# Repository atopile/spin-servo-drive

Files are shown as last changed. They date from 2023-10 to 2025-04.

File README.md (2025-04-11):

# Servos are dope.

Compared to the steppers we stick on our 3D printers, CNC machines and paintball turrets:
 - They're way faster 🏃
 - Far more powerful (higher torque for longer) 💪
 - More accurate (higher resolution) 🎯
 - And they're closed loop (they know where they are) 🤖

The only downside is that they're expensive, like hundreds of dollars.

Introducing spin ✨ - the $30 servo for the masses (designed with atopile)

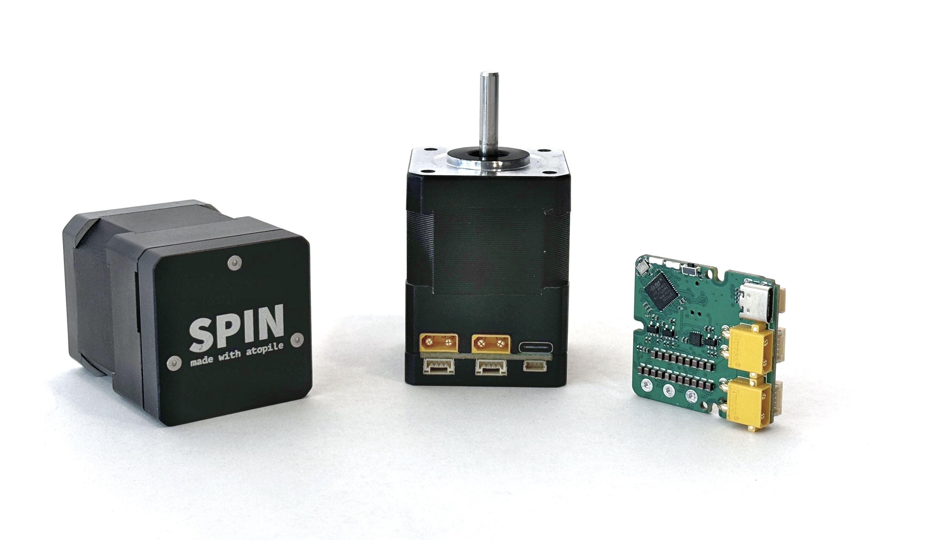
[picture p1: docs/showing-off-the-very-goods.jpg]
spin


## Wiggle wiggle wiggle

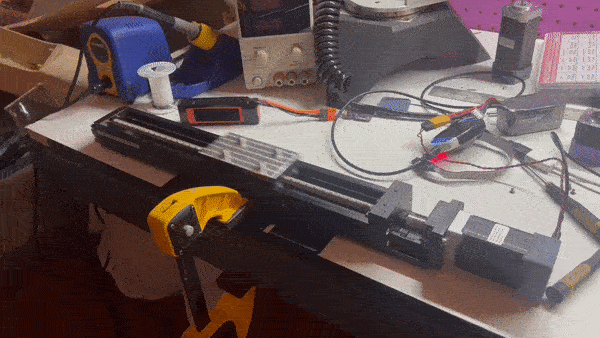
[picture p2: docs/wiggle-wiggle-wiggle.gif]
wiggle-wiggle-wiggle


## Build your own Spin Servo Motor Drive

This project is fully open source and designed with [atopile](https://github.com/atopile/atopile), a new language and compiler to design electronics with code.

## Goals + (default) Specs

- Obviously better option than stepper motors for 3D printers, CNC machines and robotics
- Open-source design that is easy to:
  - contribute to
  - fork maintainable derivatives of
  - robust

- 2x CAN comms with JST-GH connectors
- XT30 power connector
- 0.25Nm continuous rated torque (0.75Nm peak)
- <0.1° resolution
- 12V-24V input voltage

## Getting started

This project was written in `ato`, a new electronics description language we are developing to help create and share electronic designs. Get started here: https://atopile.io/

### Electronics

**Write me please!**

### Firmware

Install [PlatformIO](https://platformio.org/) into VSCode. It has the utilities to build, upload and debug the firmware.

You may also need to install `libusb` (eg. `brew install libusb` on OSx) to run the build!

There are a few build configurations:
- `debug` is intended as a JTAG configuration and includes symbols to run the debugger.
- `dfu-manual` uses the GNU command-line dfu-utility to trigger the upload via USB (**Recommended USB workflow**)
- `dfu` uses the built-in PlatformIO dfu utility to program via USB (which **I struggled with on OSx**)

To run a build either use the sidebar (easiest IMO) or PlatformIO CLI (`pio run --help`).

#### Side-bar

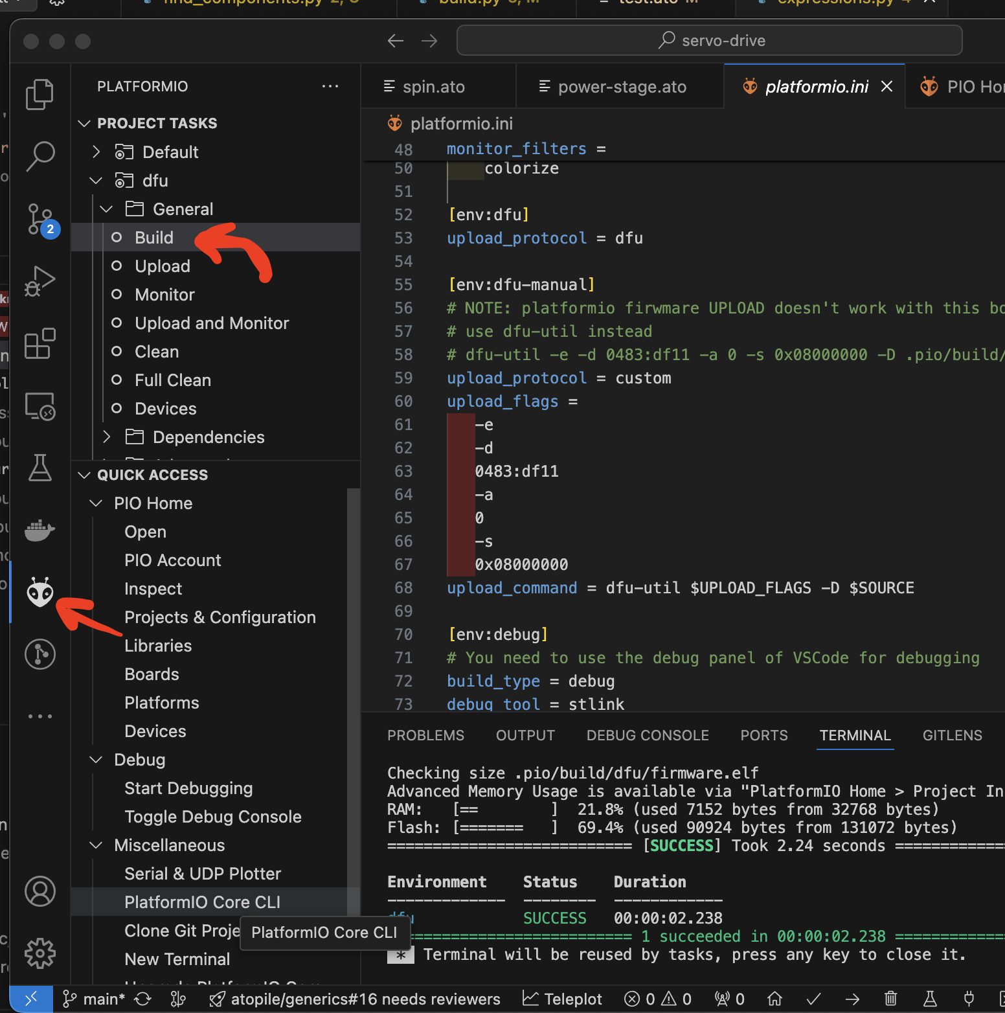
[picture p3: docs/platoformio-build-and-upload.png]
platformio


#### CLI

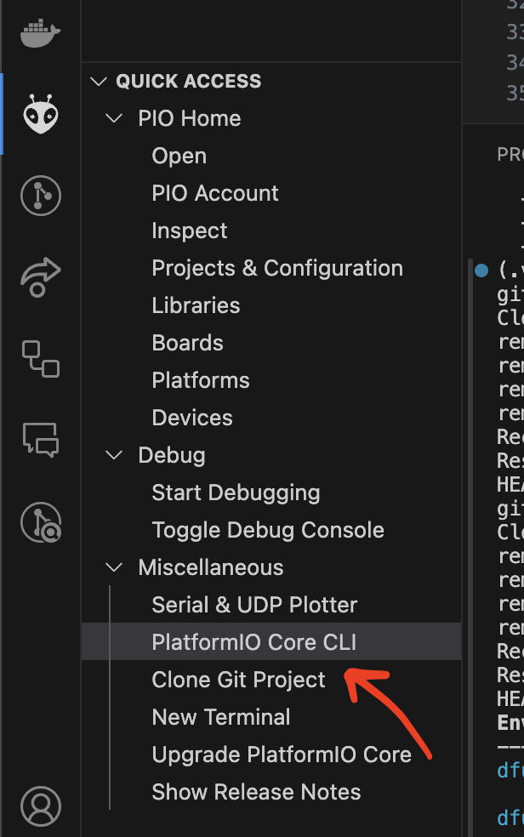
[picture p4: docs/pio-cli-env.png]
platformio-cli


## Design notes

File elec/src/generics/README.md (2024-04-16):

# Generics

## Overview

Standard libaries for use in your projects. These include:

- **Resistors**
- **Capacitors**
- **Inductors**
- **Diodes**
- **Transistors**
- **Interfaces**

## Installation
Run in the terminal:

```ato install generics``

Add to your ato project:

- Resistors   ```import Resistor from "generics/resistor.ato```
- Capacitors  ```import Capacitor from "generics/capacitor.ato```
- Inductors   ```import Inductor from "generics/inductor.ato```
- Interfaces  ```import Interface from "generics/interface.ato```
- etc...

## Features
### Resistors
The standard libary includes several thousand resistor options. In your ato project, simply specify any requirements and the best resistor will be automatically selected.
Example:

```import Resistor from "generics/resistor.ato"```
```myResistor = new Resistor```
```myResistor.value = 1000```
```myResistor.footprint = "R0402"```
```myResistor.tolerance = 10```

The solver will find a resistor that has a resistance between 900 and 1100 ohms accounting for tolerance, and a footprint of R0402.

### Capacitors
Similar to resistors, just specify the value and footprint and the solver will find the best capacitor for your application.

### Inductors
Currently not supported for automatic selection, but you can install any inductor you like using '''ato install''' and then use it in your project.

We strongly reccomend using subclassing for new components, something like this:

```import Inductor from "generics/inductor.ato"```
```component MyInductor from Inductor:```
```    value = 1000```
```    footprint = "L0402" ```

Then you can use it in your project like this:

```import MyInductor from "myInductor.ato"```
```myInductor = new MyInductor```
```myInductor.value = 1000```
```myInductor.footprint = "L0402"```

### Interfaces
Interfaces standardize the way you connect to modules. By implementing an interface from the standard libary, you can be sure that your module will be compatible with any other module that implements the same interface. This makes it easy to share modules between projects and be sure that they will work together.

## Contributing

We welcome contributions and suggestions to improve this module. Please submit your contributions as pull requests on our GitHub repository.

## License

This package documentation is provided under the [MIT License](#).

## Contact

For further inquiries or support, please contact us at [email@example.com](mailto:email@example.com).

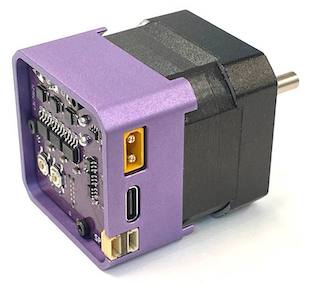
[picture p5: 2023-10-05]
docs/showing-off-the-goods.jpg

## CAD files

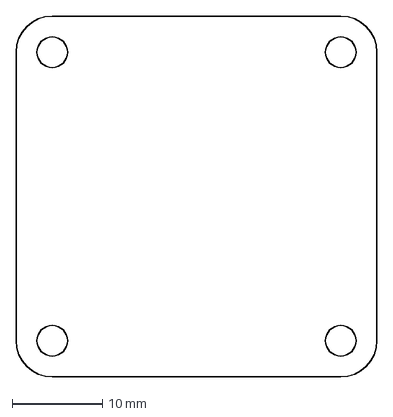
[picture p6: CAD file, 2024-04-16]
elec/src/programming-headers/mech/template_40x40 2.dxf
40.0 x 40.0 mm

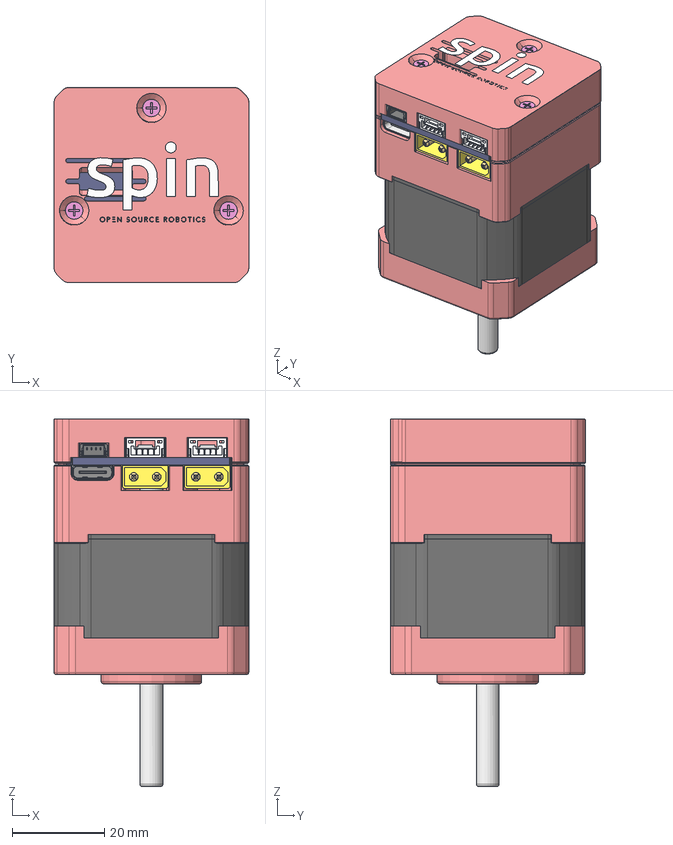
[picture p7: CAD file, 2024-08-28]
mech/SPIN.step
42.3 x 42.4 x 82.6 mm
shaft
motor_housing
lid x 2
JST SH, 4 Pin v2
Amass_XT30PW-M_pcb solder x 2
ConPins
PcbPins
Mold
Frame
SM04B-GHS-TB x 2
magnet
M2x14 x 3
hex_socket_button_head_M3x40 x 4

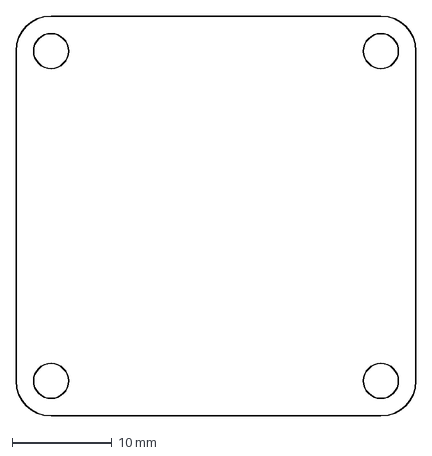
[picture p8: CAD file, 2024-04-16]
elec/src/saleae-header/mech/template_outline.dxf
40.0 x 40.0 mm

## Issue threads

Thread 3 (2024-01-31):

Buck gets hot + should be replaced with the one from the regulators lib

mawildoer, 2024-01-31:
It's commented out as of now, but needs to be reinstated https://github.com/atopile/spin-servo-drive/pull/2/files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

mawildoer, 2024-03-07:
Requires validation; have debug build of that

napowderly, 2024-05-02:
Inductor sized incorrectly on first build, updated in next rev.

Closed 2024-05-02.

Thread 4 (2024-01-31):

Boot button should enable DFU

napowderly, 2024-01-31:
Currently the boot selection pin is used for I2C, need to find a better pinout

napowderly, 2024-05-02:
Fixed, holding button on boot will enter DFU

Closed 2024-05-02.

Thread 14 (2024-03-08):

CAN on wrong micro pins

mawildoer, 2024-03-08:
CAN can't work on these pins and they don't match where we previously had it

https://www.st.com/resource/en/datasheet/stm32g431c6.pdf#page=56

```
    # CANBUS Comms
    can_ttl.rx ~ ic.PB5
    can_ttl.tx ~ ic.PB6
```

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

napowderly, 2024-05-02:
Updated in beta build

Closed 2024-05-02.

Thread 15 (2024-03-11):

Current sense not working

napowderly, 2024-03-11:
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

Moved phase C to PA3 and seems to be working well

napowderly, 2024-05-02:
Pinout updated

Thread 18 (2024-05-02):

CAN bus control - Position, Velocity, Torque

napowderly, 2024-05-02:
Objective: Build a simple interface to send commands + receive status messages from motors.

SimpleFOC has a commander interface that will currently take serial commands
https://docs.simplefoc.com/commander_interface

Want to be as standard as possible, a few possible standards to follow/integrate with:
https://opencyphal.org/
https://legacy.uavcan.org/Specification/7._List_of_standard_data_types/
https://docs.odriverobotics.com/v/0.5.4/commands.html
https://github.com/mjbots/moteus/blob/main/docs/reference.md

mawildoer, 2024-07-18:
Selected CANSimple. Implementing w/ #37

Closed 2024-07-18.

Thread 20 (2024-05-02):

Change position sensor to something more available

napowderly, 2024-05-02:
MA732 has been a little hard to source

current sensor:
14-bit, 60krpm, $2~$5 (unstable) 0 stock
https://jlcpcb.com/partdetail/Monolithic_PowerSystems-MA732GQZ/C3824836

a few alternatives:

21-Bit, 120krpm, $3.89, 1k+ stock
https://jlcpcb.com/partdetail/MagnTek-MT6835GTSTD/C2932578

14-bit, 25krpm, $2.04, 1k+ stock
https://jlcpcb.com/partdetail/MagnTek-MT6816CTSTD/C2925077

14-bit, 28krpm, $3.08, 800 stock
https://jlcpcb.com/partdetail/Ams-AS5047PATSM/C962063

Closed 2024-07-18.

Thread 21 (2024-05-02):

CAN address enumeration

napowderly, 2024-05-02:
Goal: super quickly enumerate devices, ideally without flashing new FW or requiring PC connection.

Imagining with button + LEDs, the user could toggle between colors representing different addresses. The state should be saved in non-volatile memory, so the address is preserved after power cycling.

This would be useful for applications where the user writes controller code on an RPI or Arduino and wants an easy way to reference the motors.

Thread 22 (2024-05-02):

Motion profiles

napowderly, 2024-05-02:
For applications like 3D printers and CNC machines, having a lookahead feature on the controller that can then send the next series of points to the servo could be neat.

Copper280Z has been playing around with a Klipper integration for SimpleFOC, could be a good starting place.

mawildoer, 2024-07-18:
Depends on #37

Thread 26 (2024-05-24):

Manually test current sense

napowderly, 2024-05-24:
Manual validation of current sensor.

Procedure:
1. Directly attach wires across shunt
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

2. Source current with PSU

4. Measure output of opamp circuit with Saleae

5. Read ADC value from micro

Phase A:
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

Phase B:

Phase C:

Closed 2024-07-18.

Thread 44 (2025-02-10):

Am I missing something!

kzali, 2025-02-10:
Is the motor a modified Nema 17 motor or a an actual BLDC motor? And how are the 3 phases wired?

mawildoer, 2025-02-11:
It's an actual BLDC motor in a NEMA 17 frame, which is frequently also used for stepper motors

@napowderly may know how the 3 phases are wired

kzali, 2025-02-11:
thanks that makes sense.  Great work

Closed 2025-02-11.

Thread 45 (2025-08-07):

It is posible to used pmsm motor 220v??

artayasa, 2025-08-07:
Hi mate interestjng with your project, its posible to used for ac servo pmsm 220v with coustem hardware??

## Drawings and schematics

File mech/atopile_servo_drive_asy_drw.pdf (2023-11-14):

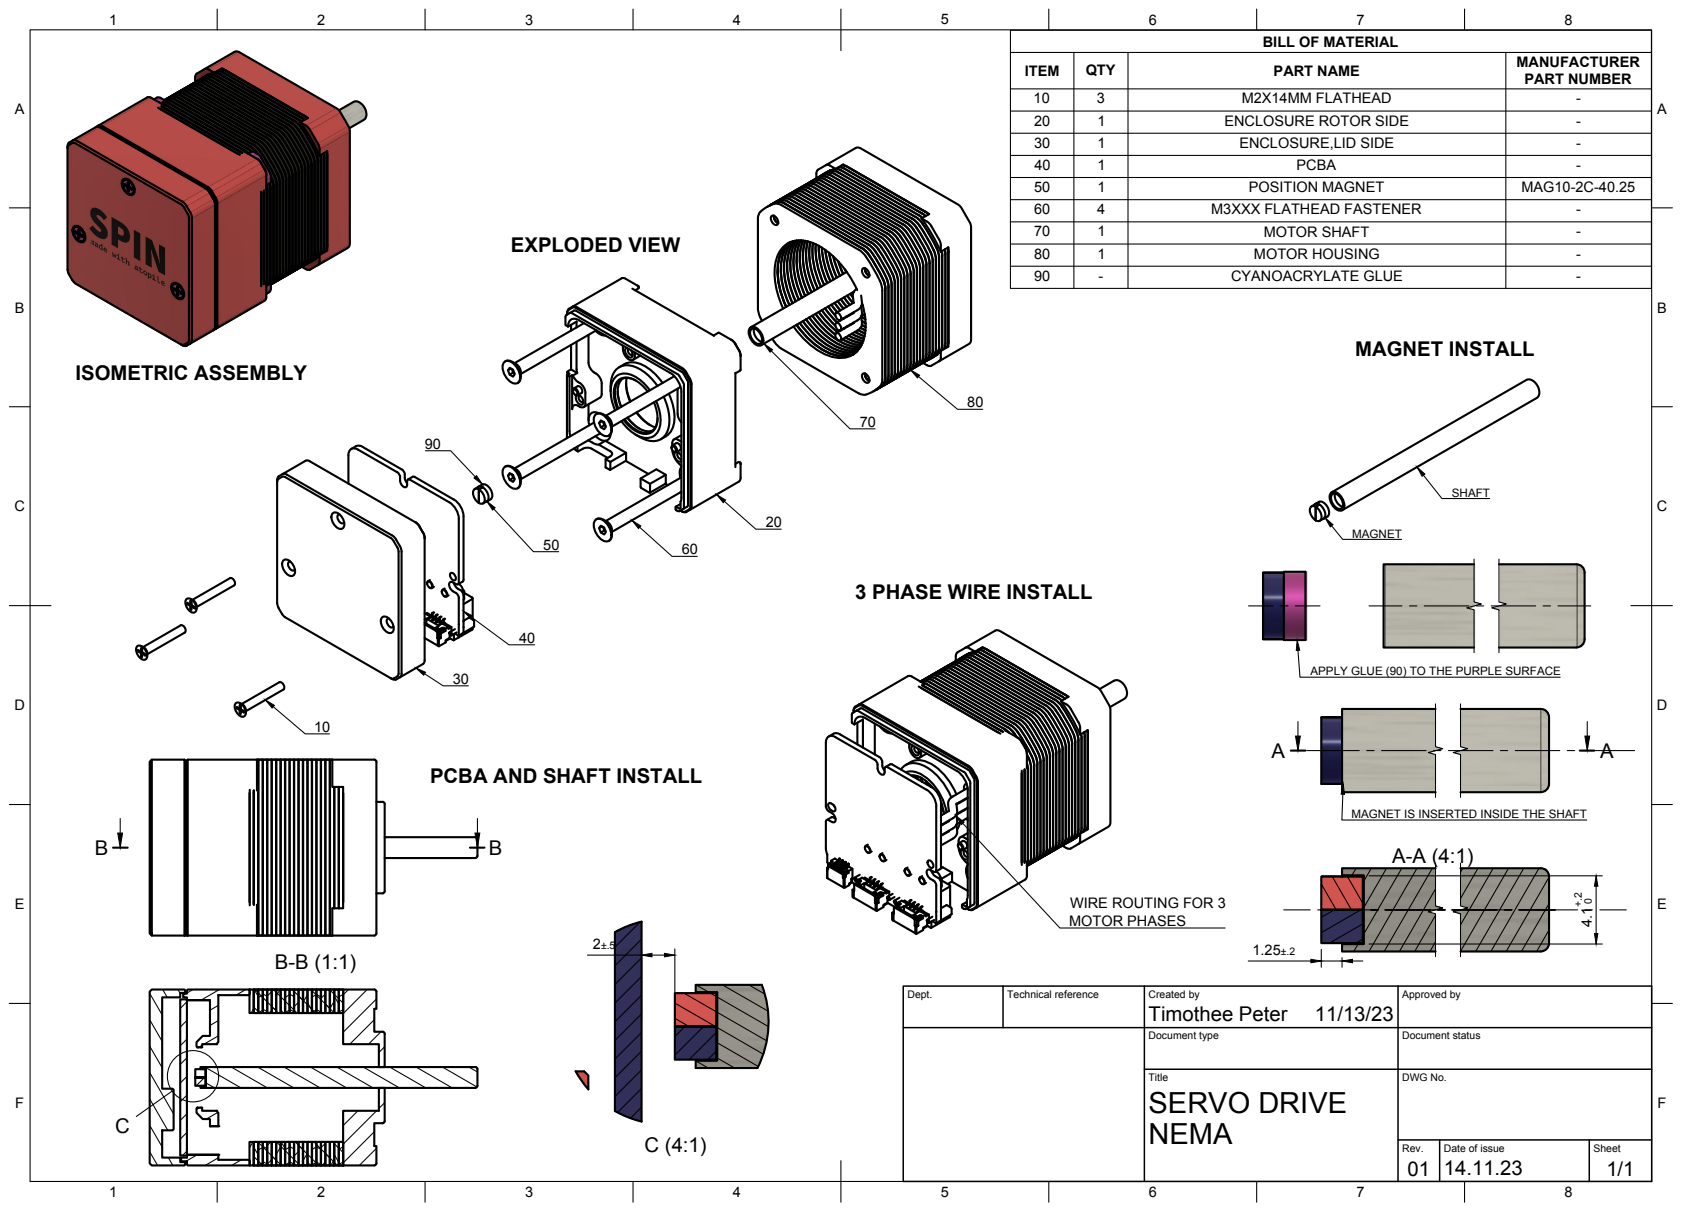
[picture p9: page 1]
Title; DWG No.; Rev.; Date of issue; Sheet; SERVO DRIVE; ITEM; QTY; PART NAME; MANUFACTURER; PART NUMBER; M2X14MM FLATHEAD; ENCLOSURE ROTOR SIDE; ENCLOSURE,LID SIDE; PCBA; POSITION MAGNET; MAG10-2C-40.25; M3XXX FLATHEAD FASTENER; MOTOR SHAFT; MOTOR HOUSING; CYANOACRYLATE GLUE; WIRE ROUTING FOR 3; MOTOR PHASES; MAGNET INSTALL; EXPLODED VIEW; ISOMETRIC ASSEMBLY

BILL OF MATERIAL

3 PHASE WIRE INSTALL

APPLY GLUE (90) TO THE PURPLE SURFACE

PCBA AND SHAFT INSTALL

MAGNET IS INSERTED INSIDE THE SHAFT

Dept. | Technical reference | Created by Timothee Peter 11/13/23 | Approved by

Document type | Document status

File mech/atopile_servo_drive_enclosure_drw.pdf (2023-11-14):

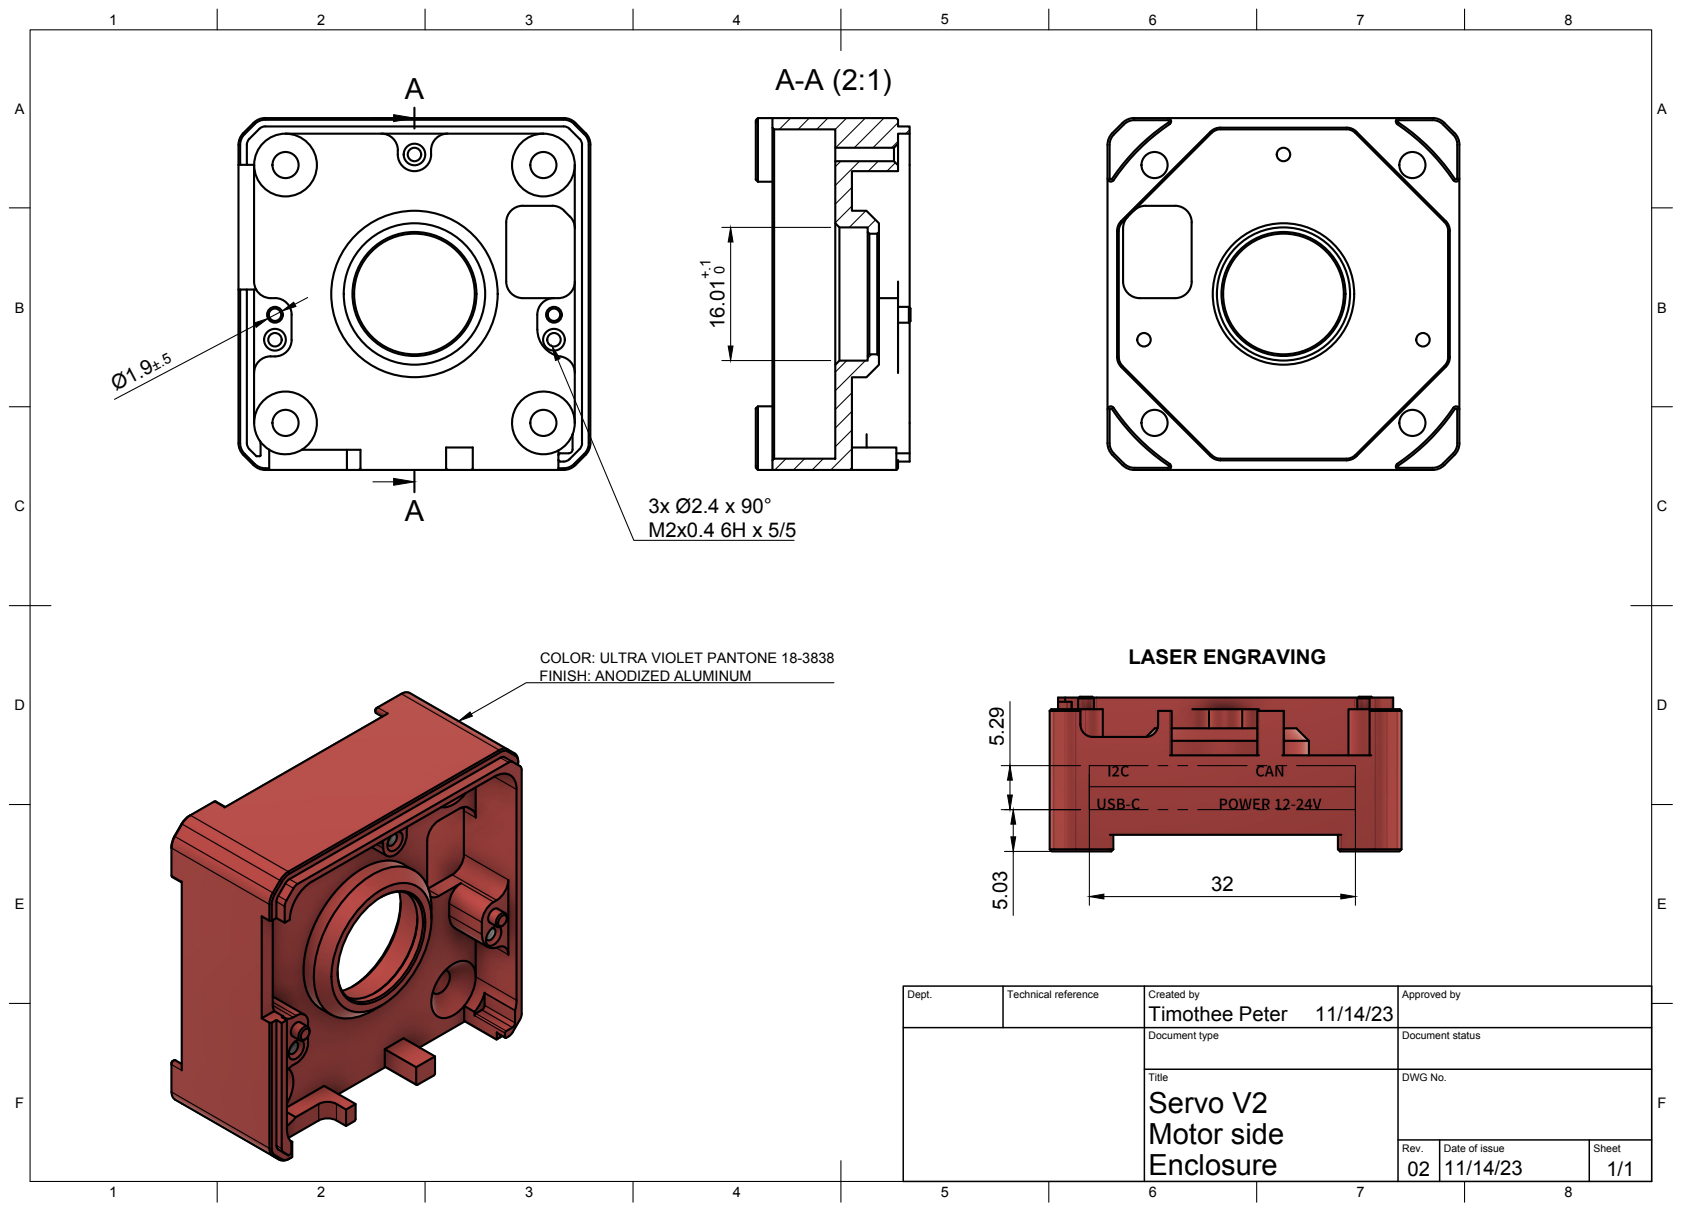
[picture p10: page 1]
Title; DWG No.; Rev.; Date of issue; Sheet; Motor side; Servo V2; LASER ENGRAVING

COLOR: ULTRA VIOLET PANTONE 18-3838
FINISH: ANODIZED ALUMINUM

Dept. | Technical reference | Created by Timothee Peter 11/14/23 | Approved by

Document type | Document status

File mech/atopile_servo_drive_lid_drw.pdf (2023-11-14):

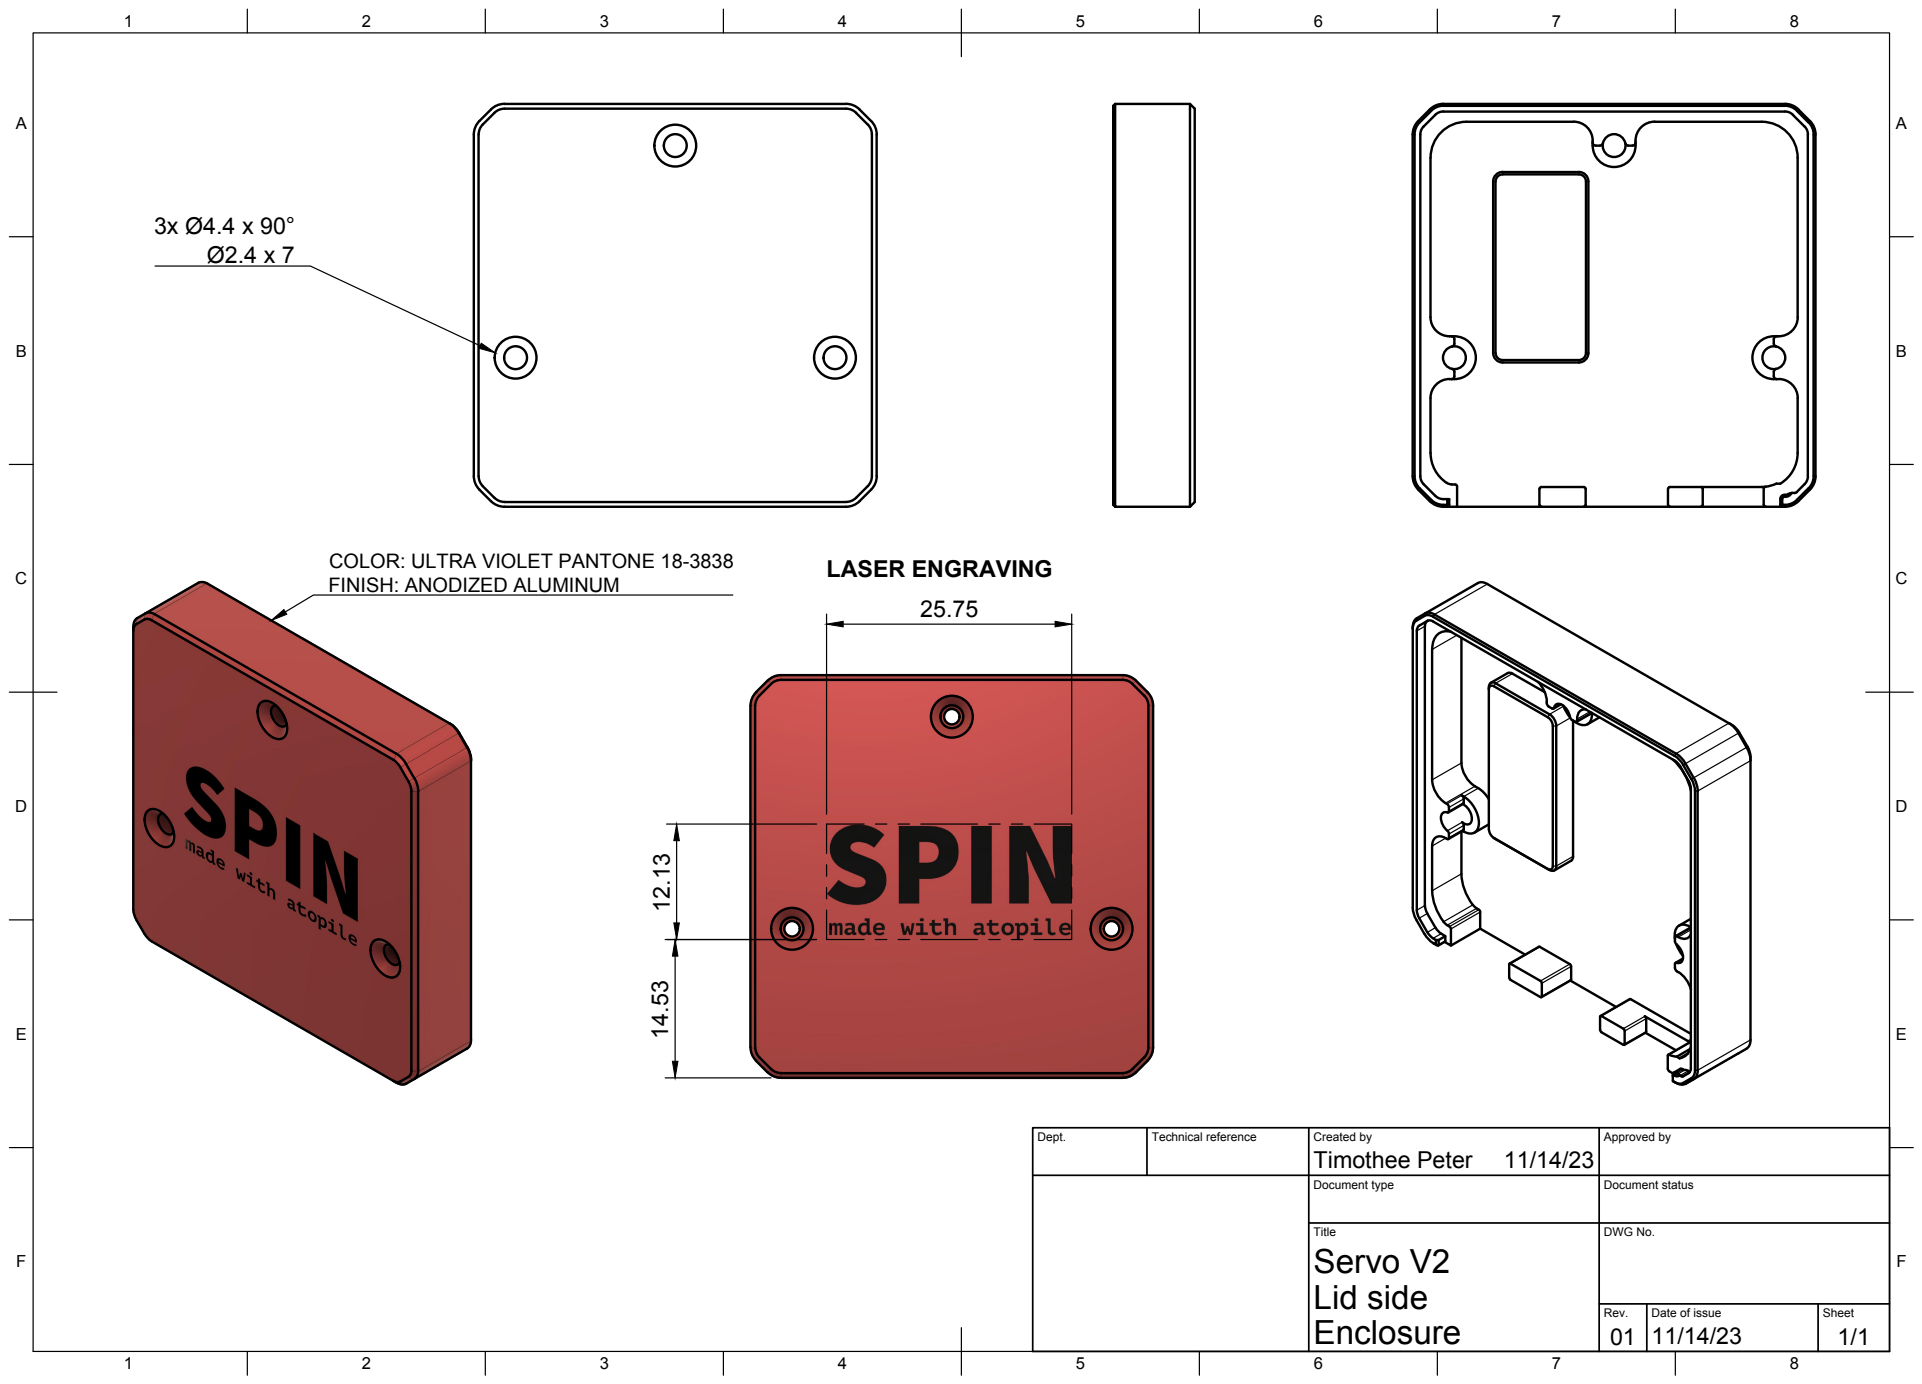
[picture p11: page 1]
Title; DWG No.; Rev.; Date of issue; Sheet; Lid side; Servo V2; COLOR: ULTRA VIOLET PANTONE 18-3838; LASER ENGRAVING

FINISH: ANODIZED ALUMINUM

Dept. | Technical reference | Created by Timothee Peter 11/14/23 | Approved by

Document type | Document status

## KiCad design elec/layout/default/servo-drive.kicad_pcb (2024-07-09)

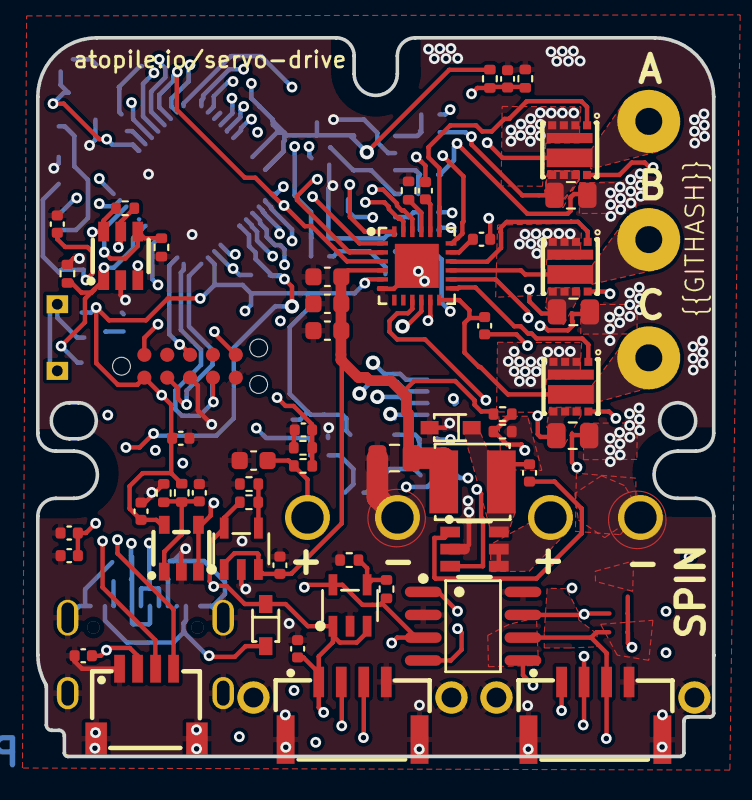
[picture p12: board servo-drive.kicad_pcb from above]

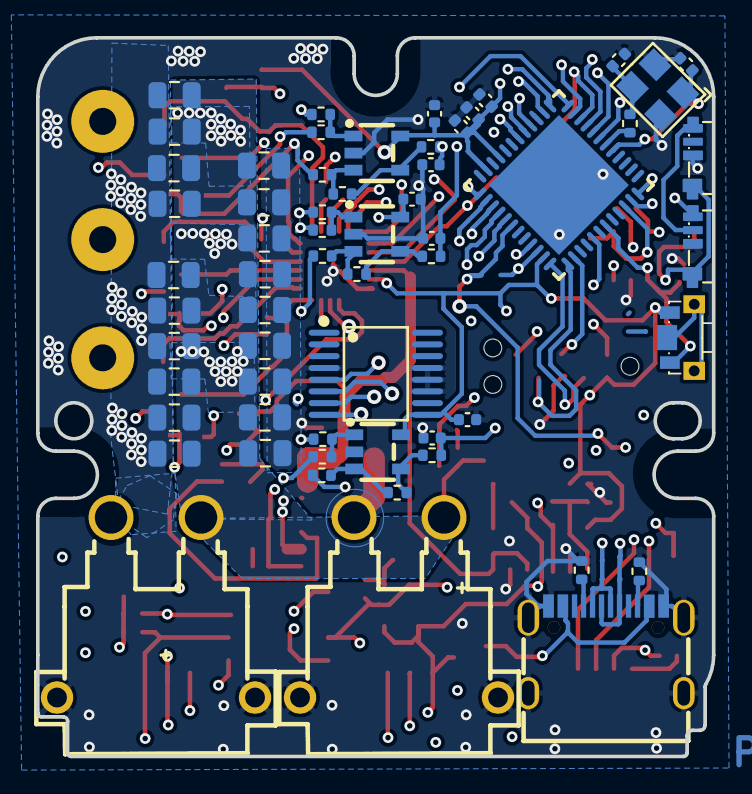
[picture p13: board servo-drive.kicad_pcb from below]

Board: 4 copper layers, 37.6 x 39.9 mm, 125 parts (60 on the bottom side), 80 nets.

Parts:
C1: 10V 10uF X5R ±10% 0603 Multilayer Ceramic Capacit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; C0603
C2, C13, C16, C17, C18, C19, C24, C28, C40, C51: 16V 100nF X7R ±10% 0402 Multilayer Ceramic Capaci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; C0402
C3, C4, C6, C20, C21, C22, C25, C26, C27, C29, C30, C35, C36, C37, C38, C39, C47, C48, C49: C0805
C5, C7, C9, C14, C15, C33, C34, C41, C43, C45, C50: 25V 1uF X5R ±10% 0402 Multilayer Ceramic Capacito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; C0402
C8: 25V 10uF X5R ±10% 0805 Multilayer Ceramic Capacit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; C0805
C10, C11, C12: 50V 2.2nF X7R ±10% 0402 Multilayer Ceramic Capaci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; C0402
C23, C31, C32: 16V 4.7uF X5R ±10% 0603 Multilayer Ceramic Capaci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; C0603
C42, C44: 50V 22pF C0G ±5% 0402 Multilayer Ceramic Capacito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; C0402
J1: USB-C-SMD_KH-TYPE-C-16P
R1, R15, R20, R38: 62.5mW Thick Film Resistors 50V ±100ppm/℃ ±1% 10k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; R0402
R2, R6, R13, R25, R44, R48, R50: 62.5mW Thick Film Resistors 50V ±100ppm/℃ ±1% 1kΩ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; R0402
R3: 62.5mW Thick Film Resistors 50V ±100ppm/℃ ±1% 100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; R0402
R4, R8, R47: 3mΩ +/- 1%; R0805
R5, R9: 62.5mW Thick Film Resistors 50V ±100ppm/℃ ±1% 5.1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; R0402
R7: 62.5mW Thick Film Resistors 50V ±100ppm/℃ ±1% 200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; R0402
R10: 62.5mW Thick Film Resistors 50V ±100ppm/℃ ±1% 27.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; R0402
R11: 62.5mW Thick Film Resistors 50V ±100ppm/℃ ±1% 3kΩ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; R0402
R12, R14, R26, R45, R49, R51: 62.5mW Thick Film Resistors 50V ±100ppm/℃ ±1% 47k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; R0402
R16, R46, R52: 62.5mW Thick Film Resistors 50V -200ppm/℃~+500ppm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; R0402
R17: 62.5mW Thick Film Resistors 50V ±100ppm/℃ ±1% 20.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; R0402
R18: 62.5mW Thick Film Resistors 50V ±1% ±200ppm/℃ 6.3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; R0402
R19: 10kohm +/- 1%; R0402
R21: 62.5mW Thick Film Resistors 50V ±100ppm/℃ ±1% 11.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; R0402
R22: 62.5mW Thick Film Resistors 50V ±100ppm/℃ ±1% 6.2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; R0402
R29: 62.5mW Thick Film Resistors 50V ±100ppm/℃ ±1% 41.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; R0402
R30: 62.5mW Thick Film Resistors 50V ±100ppm/℃ ±1% 4.3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; R0402
R31: 62.5mW Thick Film Resistors 50V ±100ppm/℃ ±1% 43k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; R0402
U1, U3, U28: V-DFN3030-8K_L3.0-W3.0-P0.65-BL
U2, U14: CONN-TH_XT30PW-M
U4, U20, U21, U24: SOT-23-5_L3.0-W1.7-P0.95-LS2.8-BR
U5, U32: LED-SMD_4P-L4.0-W1.4_SK6805SIDE-S
U6, U18: SOT-23-6_L2.9-W1.6-P0.95-LS2.8-BR
U7, U8, U9: OutputPad
U10: IND-SMD_L4.0-W4.0
U11: KEY-SMD_SKTDLDE010
U12: VQFN-24_L4.0-W4.0-P0.50-TL-EP2.5
U13: UFQFPN-48_L7.0-W7.0-P0.50-BL-EP
U15: CONN-SMD_4P-P1.00_SM04B-SRSS-TB-LF-SN
U16: TAG-CONNECT_TC2050-IDC
U17, U19, U31, U33, U34, U35: NetTie-2_SMD_Pad0.25mm
U22, U23: SOT-23-5_L3.0-W1.7-P0.95-LS2.8-BL
U25: SOIC-8_L4.9-W3.9-P1.27-LS6.0-BL
U26, U27: CONN-SMD_4P-P1.25_SM04B-GHS-TB-LF-SN
U29: TSSOP-16_L5.0-W4.4-P0.65-LS6.4-BL
U30, U36: SOD-323_L1.8-W1.3-LS2.5-RD
U37: OSC-SMD_4P-L3.2-W2.5-BL

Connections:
anchor: U11.3, U11.4
canh: U25.7, U26.2, U27.2
canl: U25.6, U26.3, U27.3
cb: C24.1, U6.1
cc1: J1.A5, R5.1
cc2: J1.B5, R9.1
cs: U13.25, U29.8
dm: J1.A7, J1.B7, U13.33
dp: J1.A6, J1.B6, U13.34
ios.led1-vcc: U5.3, U32.4
micro-miso: U13.27, U29.5
micro-mosi: U13.28, U29.6
micro-sda: U13.30, U15.3
micro-vcc: U5.4, U13.29
micro-vcc-1: R20.2, U11.1, U13.43, U18.1
micro-vcc-2: C28.1, R15.2, R19.1, U13.12
micro-vcc-3: C19.1, R10.2, R11.1, U13.13
micro.micro-io: R2.1, U13.46, U18.4
micro.micro-io-1: R3.1, U13.14, U18.6
micro.micro.ic-vcc-1: C42.1, U13.5, U37.1
pf1_osc_out: R7.1, U13.6
power_stage-gnd: C1.2, C2.2, C3.2, C4.2, C5.2, C6.2, C7.2, C8.2, C9.2, C10.2, C11.2, C12.2, C13.2, C14.2, C15.2, C16.2, C17.2, C18.2, C19.2, C20.2, C21.2, C22.2, C23.2, C25.2, C26.2, C27.2, C28.2, C29.2, C30.2, C31.2, C32.2, C33.2, C34.2, C35.2, C36.2, C37.2, C38.2, C39.2, C40.2, C42.2, C44.2, C47.2, C48.2, C49.2, C50.2, C51.2, J1.1, J1.2, J1.3, J1.4, J1.A1, J1.A12, J1.B1, J1.B12, R2.2, R4.2, R5.2, R8.2, R9.2, R11.2, R18.2, R19.2, R20.1, R22.2, R30.2, R31.2, R38.2, R47.2, U2.1, U2.3, U2.4, U4.2, U5.2, U6.2, U12.6, U12.25, U13.49, U14.1, U14.3, U14.4, U15.1, U15.5, U15.6, U16.3, U16.5, U18.2, U19.2, U20.2, U21.2, U22.2, U23.2, U24.2, U25.2, U25.8, U26.4, U26.5, U26.6, U27.4, U27.5, U27.6, U29.4, U29.11, U29.12, U29.13, U32.2, U33.2, U35.2, U36.2, U37.2, U37.4
power_stage-vcc: C1.1, C3.1, C4.1, C6.1, C20.1, C21.1, C22.1, C25.1, C26.1, C27.1, C29.1, C30.1, C35.1, C36.1, C37.1, C38.1, C39.1, C47.1, C48.1, C49.1, R10.1, U1.2, U1.3, U1.4, U1.10, U2.2, U3.2, U3.3, U3.4, U3.10, U6.4, U6.5, U14.2, U28.2, U28.3, U28.4, U28.10
power_stage-vcc-1: C5.1, C8.1, C23.1, C31.1, C32.1, R29.1, U10.2, U12.4, U22.1, U22.3
power_stage-vcc-2: C7.1, C13.1, C15.1, C16.1, C17.1, C18.1, C40.1, C50.1, C51.1, R1.1, R3.2, R15.1, R21.1, U4.5, U11.2, U12.5, U13.20, U13.21, U13.23, U13.35, U13.48, U15.2, U16.1, U18.5, U20.5, U21.5, U23.5, U24.5, U25.3, U29.9
power_stage.gate_driver.ic-vcc: C41.1, U12.20
power_stage.gate_driver.ic-vcc-1: C43.1, U12.17
power_stage.gate_driver.ic-vcc-2: C45.1, U12.14
power_stage.gate_driver.ic-vcc-3: R31.1, U12.21
power_stage.phase_a-vcc: U12.1, U12.22, U13.8
power_stage.phase_a.current_sensor-vcc: R14.2, R45.2, R51.2, U4.3, U4.4
power_stage.phase_a.current_sensor-vcc-1: C10.1, R16.2, U13.17
power_stage.phase_a.current_sensor.net_tie_n-_shunt_n: R6.1, U19.1
power_stage.phase_a.current_sensor.net_tie_p-_shunt_p: R13.1, U17.1
power_stage.phase_a.current_sensor.opamp-gnd: R12.2, R16.1, U20.4
power_stage.phase_a.current_sensor.opamp-inverting: R6.2, R12.1, U20.3
power_stage.phase_a.current_sensor.opamp-non_inverting: R13.2, R14.1, U20.1
power_stage.phase_a.half_bridge-gnd: R4.1, U17.2, U28.5, U28.6, U28.7
power_stage.phase_a.half_bridge-io: C41.2, U7.1, U12.18, U28.9
power_stage.phase_a.half_bridge-vcc: U12.19, U28.1
power_stage.phase_a.half_bridge-vcc-1: U12.11, U28.8
power_stage.phase_b-vcc: U12.2, U12.23, U13.9
power_stage.phase_b.current_sensor-vcc: C11.1, R46.2, U13.18
power_stage.phase_b.current_sensor.net_tie_n-_shunt_n: R25.1, U33.1
power_stage.phase_b.current_sensor.net_tie_p-_shunt_p: R44.1, U31.1
power_stage.phase_b.current_sensor.opamp-gnd: R26.2, R46.1, U21.4
power_stage.phase_b.current_sensor.opamp-inverting: R25.2, R26.1, U21.3
power_stage.phase_b.current_sensor.opamp-non_inverting: R44.2, R45.1, U21.1
power_stage.phase_b.half_bridge-gnd: R8.1, U1.5, U1.6, U1.7, U31.2
power_stage.phase_b.half_bridge-io: C43.2, U1.9, U8.1, U12.15
power_stage.phase_b.half_bridge-vcc: U1.1, U12.16
power_stage.phase_b.half_bridge-vcc-1: U1.8, U12.10
power_stage.phase_c-vcc: U12.3, U12.24, U13.10
power_stage.phase_c.current_sensor-vcc: C12.1, R52.2, U13.11
power_stage.phase_c.current_sensor.net_tie_n-_shunt_n: R48.1, U35.1
power_stage.phase_c.current_sensor.net_tie_p-_shunt_p: R50.1, U34.1
power_stage.phase_c.current_sensor.opamp-gnd: R49.2, R52.1, U24.4
power_stage.phase_c.current_sensor.opamp-inverting: R48.2, R49.1, U24.3
power_stage.phase_c.current_sensor.opamp-non_inverting: R50.2, R51.1, U24.1
power_stage.phase_c.half_bridge-gnd: R47.1, U3.5, U3.6, U3.7, U34.2
power_stage.phase_c.half_bridge-io: C45.2, U3.9, U9.1, U12.12
power_stage.phase_c.half_bridge-vcc: U3.1, U12.13
power_stage.phase_c.half_bridge-vcc-1: U3.8, U12.9
power_stage.voltage_reference.opamp-non_inverting: C2.1, R1.2, R38.1, U4.1
power_supply-vcc: J1.A4, J1.A9, J1.B4, J1.B9, U30.2
power_supply-vcc-1: C9.1, C14.1, C33.1, C34.1, R17.1, U5.1, U22.5, U23.1, U23.3, U26.1, U27.1, U30.1, U32.1
power_supply.buck.feedback_div-out: R29.2, R30.1, U6.3
power_supply.ldo3V3.feedback_div-out: R21.2, R22.1, U23.4
power_supply.ldo5V.feedback_div-out: R17.2, R18.1, U22.4
reset: U13.7, U16.10
rx: U18.3, U25.4
sck: U13.26, U29.7
scl: U13.16, U15.4
sw: C24.2, U6.6, U10.1, U36.1
tck: U13.37, U16.4
tdi: U13.38, U16.8
tdo: U13.41, U16.6
tms: U13.36, U16.2
tx: U13.47, U25.1
xout: C44.1, R7.2, U37.3

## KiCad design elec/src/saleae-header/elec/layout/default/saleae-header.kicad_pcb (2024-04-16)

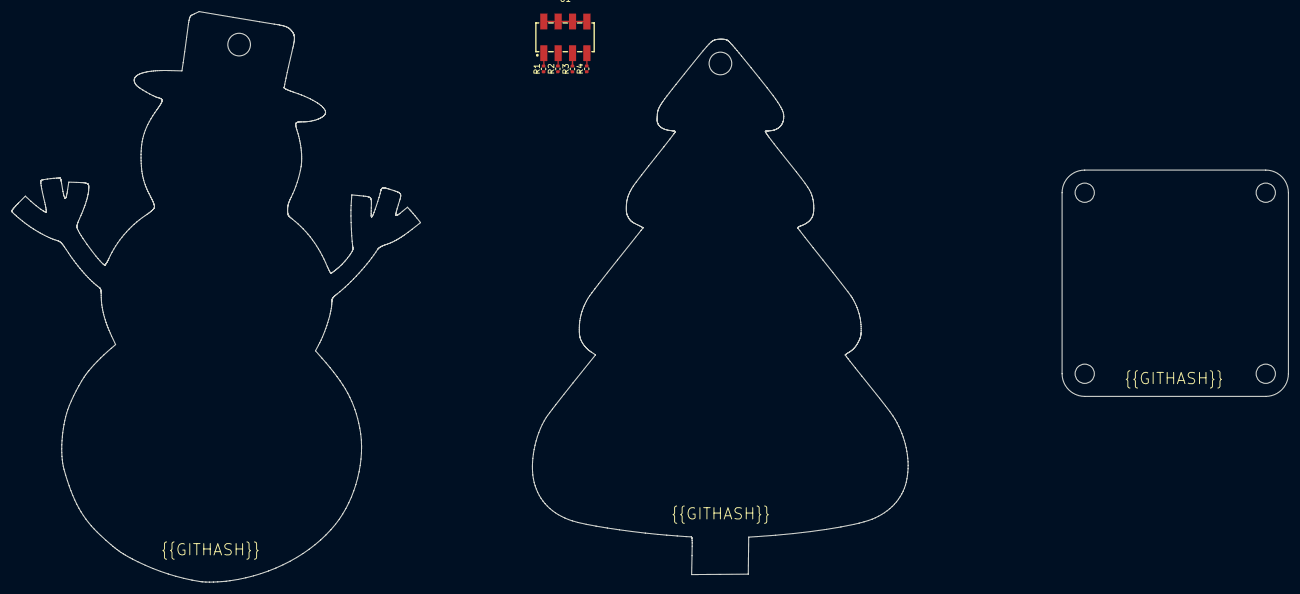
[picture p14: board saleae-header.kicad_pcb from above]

Board: 2 copper layers, 66.4 x 94.6 mm, 5 parts (0 on the bottom side), 5 nets.

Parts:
R1, R2, R3, R4: Chip Resistor - Surface Mount 1KOhms ±5% 1/16W 04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; R0402
U1: HDR-SMD_8P-P2.54-V-M-R2-C4-LS7.4

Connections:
_1: R1.2, U1.1
_3: R2.2, U1.3
_5: R3.2, U1.5
_7: R4.2, U1.7
gnd: U1.2, U1.4, U1.6, U1.8

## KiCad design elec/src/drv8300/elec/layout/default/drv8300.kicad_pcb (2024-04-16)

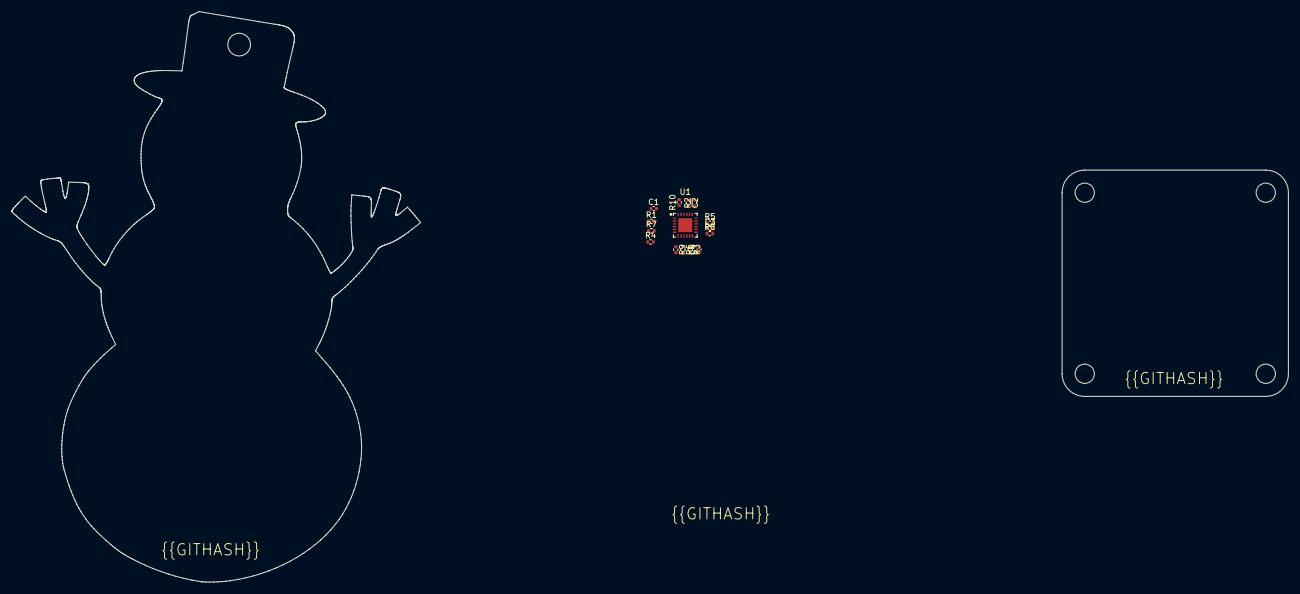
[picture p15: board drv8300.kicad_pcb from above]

Board: 2 copper layers, 15 parts (0 on the bottom side), 15 nets, no tracks yet.

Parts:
C1, C2, C3, C4: 25V 1uF X5R ±10% 0402 Multilayer Ceramic Capacito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; C0402
R1, R4, R7: Chip Resistor - Surface Mount 4.7KOhms ±5% 1/16W 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; R0402
R2, R3, R5, R6, R8, R9: Chip Resistor - Surface Mount 10Ohms ±5% 1/16W 04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; R0402
R10: Chip Resistor - Surface Mount 39KOhms ±5% 1/16W 0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; R0402
U1: VQFN-24_L4.0-W4.0-P0.50-TL-EP2.5

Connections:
gnd: R1.2, R4.2, R7.2, R10.2, U1.6, U1.25
gnd-9: C2.2, C3.2, C4.2, U1.20
vcc-1: U1.4, U1.5
vcc-6: U1.1, U1.22
vcc-7: C2.1, U1.18
vcc-8: R2.1, R2.2, U1.19
vcc-9: R3.1, U1.11
vcc-13: R10.1, U1.2, U1.23
vcc-14: C3.1, U1.15
vcc-15: R5.1, R5.2, U1.16
vcc-16: R6.1, U1.10
vcc-20: U1.3, U1.24
vcc-21: C4.1, U1.12
vcc-22: R8.1, R8.2, U1.13
vcc-23: R9.1, U1.9

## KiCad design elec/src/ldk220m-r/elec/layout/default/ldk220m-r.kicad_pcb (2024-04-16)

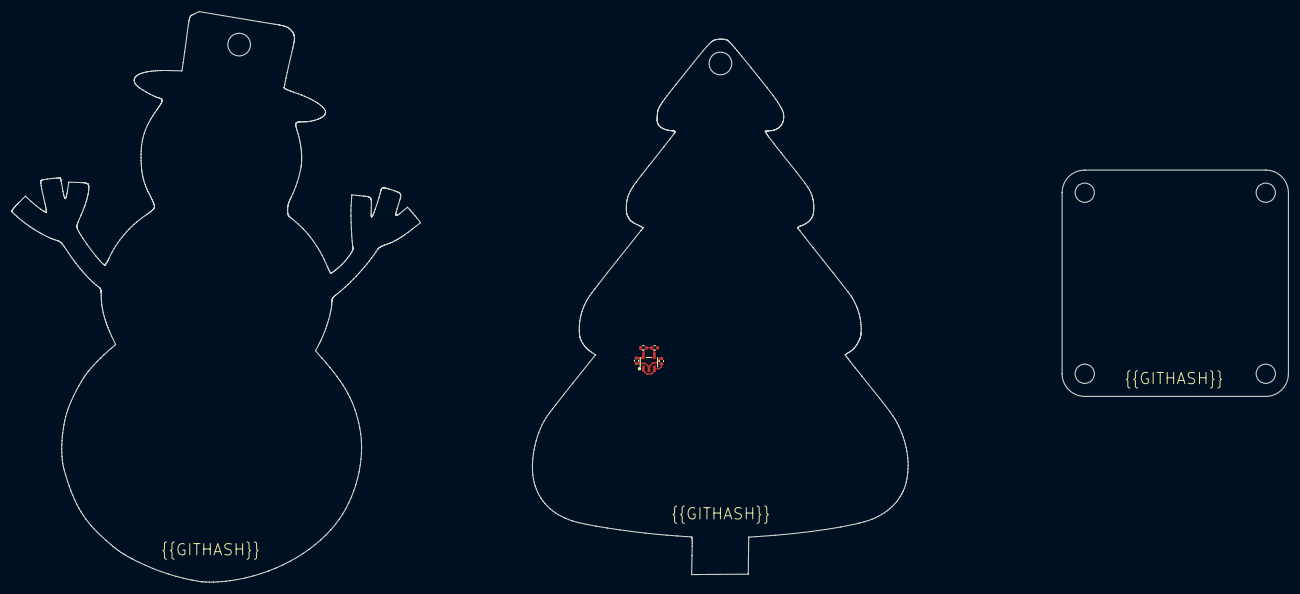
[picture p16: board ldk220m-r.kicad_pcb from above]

Board: 2 copper layers, 66.4 x 94.6 mm, 5 parts (0 on the bottom side), 4 nets.

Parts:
C1, C2: Multilayer Ceramic Capacitors MLCC - SMD/SMT 1uF 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; C0402
R1: Chip Resistor - Surface Mount 18KOhms ±5% 1/16W 0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; R0402
R2: Chip Resistor - Surface Mount 10KOhms ±5% 1/16W 0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; R0402
U1: SOT-23-5_L3.0-W1.7-P0.95-LS2.8-BL

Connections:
gnd: C1.2, C2.2, R2.2, U1.2
out: R1.2, R2.1, U1.4
vcc: C1.1, U1.1, U1.3
vcc-1: C2.1, R1.1, U1.5

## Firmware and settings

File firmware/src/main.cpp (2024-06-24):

#include <Arduino.h>
#include <SimpleFOC.h>
#include <SimpleFOCDrivers.h>
#include <Wire.h>
#include <settings/stm32/STM32FlashSettingsStorage.h>
#include <encoders/ma730/MagneticSensorMA730SSI.h>
#include <encoders/ma730/MagneticSensorMA730.h>
#include <encoders/hysteresis/HysteresisSensor.h>
#include <comms/telemetry/SimpleTelemetry.h>
#include <comms/telemetry/TeleplotTelemetry.h>
#include <utilities/stm32math/STM32G4CORDICTrigFunctions.h>


#define SERIAL_SPEED 115200

#define MUX_SELECT PA6
#define BUTTON PB5
#define BATT_VOLTAGE_SENSE PA4
#define TEMP_SENSE PA5
#define LED PC6

// Define CAN bus pins
#define CAN_TX_PIN PB9
#define CAN_RX_PIN PB8


// BLDC motor & driver instance
BLDCMotor motor = BLDCMotor(5, 5.2f, 120.0f, 0.000831f); // int pp,  float R = NOT_SET, float KV = NOT_SET, float L = NOT_SET
BLDCDriver3PWM driver = BLDCDriver3PWM(PA0, PA1, PA2);

//Position Sensor
MagneticSensorMA730 sensor = MagneticSensorMA730(PB12);
HysteresisSensor hysteresisSensor = HysteresisSensor(sensor, 0.001f);

LowsideCurrentSense current_sense = LowsideCurrentSense(0.003, 46, PB0, PB1, PA3);

// settings
STM32FlashSettingsStorage settings = STM32FlashSettingsStorage(); // use 1 page at top of flash

// instantiate the commander
Commander command = Commander(Serial);
void doMotor(char* cmd) { command.motor(&motor, cmd); };
void doSave(char* cmd) { settings.saveSettings(); };
void doLoad(char* cmd) { settings.loadSettings(); };
void doReinit(char* cmd) { motor.sensor_direction = Direction::UNKNOWN; motor.zero_electric_angle = NOT_SET; motor.initFOC(); };
void doHysteresis(char* cmd) { hysteresisSensor._amount = atof(cmd); Serial.print("Hysteresis: "); Serial.println(hysteresisSensor._amount, 4); };
void doSetSensor(char* cmd) {
  if (cmd[0]=='1') {
    motor.linkSensor(&hysteresisSensor);
    Serial.println("Using hysteresis");
  }
  else {
    motor.linkSensor(&sensor);
    Serial.println("Using MA730");
  }
};

// telemetry
TextIO textIO = TextIO(Serial);
//SimpleTelemetry telemetry = SimpleTelemetry();
TeleplotTelemetry telemetry = TeleplotTelemetry();
void doDownsample(char* cmd) { telemetry.downsample = atoi(cmd); };

void setup() {
  Serial.begin(SERIAL_SPEED);
  while (!Serial);
  SimpleFOCDebug::enable(&Serial);

  Serial.print("spin servo - firmware version ");
  Serial.println(SPIN_SERVO_FIRMWARE_VERSION);

  // Wire.setSCL(PB8);
  // Wire.setSDA(PB9);
  // Wire.begin();
  // Wire.setClock(400000);

  SPI.setMISO(PB14);
  SPI.setMOSI(PB15);
  SPI.setSCLK(PB13);


  SimpleFOC_CORDIC_Config();

  // driver config
  // power supply voltage [V]
  driver.voltage_power_supply = 10;
  driver.voltage_limit = driver.voltage_power_supply*0.95f;
  driver.pwm_frequency	= 20000;

  driver.init();
  sensor.init();
  hysteresisSensor.init();


  FieldStrength fs = sensor.getFieldStrength();
  Serial.print("Field strength: 0x");
  Serial.println(fs, HEX);

  // link driver
  motor.linkDriver(&driver);
  motor.linkSensor(&hysteresisSensor);

  // current sense
  current_sense.linkDriver(&driver);
  current_sense.init();
  motor.linkCurrentSense(&current_sense);

  // aligning voltage
  motor.voltage_sensor_align = 2;
  motor.current_limit = 3;
  motor.voltage_limit = driver.voltage_limit / 2.0f;
  motor.velocity_limit = 1000.0f; // 1000rad/s = aprox 9550rpm

  // some defaults
  motor.PID_velocity.P = 0.05f;
  motor.PID_velocity.I = 0.05f;
  motor.PID_velocity.D = 0.000f;
  motor.PID_velocity.output_ramp = 1000;
  motor.LPF_velocity.Tf = 0.01f;
  motor.P_angle.P = 20.0f;
  motor.P_angle.I = 0.0f;
  motor.P_angle.D = 0.0f;
  motor.P_angle.output_ramp = 1000;
  motor.LPF_angle.Tf = 0.005f;

  motor.torque_controller = TorqueControlType::foc_current;
  motor.controller = MotionControlType::angle;
  motor.motion_downsample = 10;

  // load settings
  settings.addMotor(&motor);
  SimpleFOCRegister registers[] = { REG_SENSOR_DIRECTION, REG_ZERO_ELECTRIC_ANGLE, REG_VEL_LPF_T, REG_VEL_PID_P, REG_VEL_PID_I, REG_VEL_PID_D, REG_VEL_PID_LIM, REG_VEL_PID_RAMP, REG_ANG_LPF_T, REG_ANG_PID_P, REG_ANG_PID_I, REG_ANG_PID_D, REG_ANG_PID_LIM, REG_ANG_PID_RAMP, REG_CURQ_LPF_T, REG_CURQ_PID_P, REG_CURQ_PID_I, REG_CURQ_PID_D, REG_CURQ_PID_LIM, REG_CURQ_PID_RAMP, REG_CURD_LPF_T, REG_CURD_PID_P, REG_CURD_PID_I, REG_CURD_PID_D, REG_CURD_PID_LIM, REG_CURD_PID_RAMP, REG_VOLTAGE_LIMIT, REG_CURRENT_LIMIT, REG_VELOCITY_LIMIT, REG_MOTION_DOWNSAMPLE, REG_TORQUE_MODE, REG_CONTROL_MODE };
  settings.setRegisters(registers, sizeof(registers)/sizeof(SimpleFOCRegister));
  settings.settings_version = 2;
  settings.init();
  //settings.loadSettings();

  // initialize motor
  motor.init();

  // align sensor and start FOC
  Serial.print("Aligning...");
  motor.initFOC();

  // add commands
  command.echo = true;
  command.add('M', doMotor, "motor commands");
  command.add('s', doSave, "save settings");
  command.add('l', doLoad, "load settings");
  command.add('d', doDownsample, "downsample telemetry");
  command.add('r', doReinit, "reinit motor");
  command.add('h', doHysteresis, "hysteresis amount");
  command.add('S', doSetSensor, "set sensor (0=MA730, 1=hysteresis)");
  // add telemetry
  telemetry.addMotor(&motor);
  telemetry.downsample = 0; // off by default, use register 28 to set
  uint8_t telemetry_registers[] = { REG_TARGET, REG_ANGLE, REG_VELOCITY, REG_SENSOR_MECHANICAL_ANGLE, REG_ITERATIONS_SEC };
  telemetry.setTelemetryRegisters(sizeof(telemetry_registers)/sizeof(SimpleFOCRegister), telemetry_registers);
  telemetry.init(textIO);

  Serial.println(F("Motor ready."));
  Serial.println(F("Set the target using serial terminal:"));
}


void loop() {
  // Motion control function
  motor.move();
  // main FOC algorithm function
  motor.loopFOC();
  // user communication
  command.run();
  // telemetry
  telemetry.run();
}

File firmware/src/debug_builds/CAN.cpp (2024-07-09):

#include <Arduino.h>
#include "SimpleCan.h"

#define CAN_MUX PA6


static void handleCanMessage(FDCAN_RxHeaderTypeDef rxHeader, uint8_t *rxData);
static void init_CAN(void);
static void Button_Down(void);


// pass in optional shutdown and terminator pins that disable transceiver and add 120ohm resistor respectively
SimpleCan can1;
SimpleCan::RxHandler can1RxHandler(8, handleCanMessage);

FDCAN_TxHeaderTypeDef TxHeader;
uint8_t TxData[8];

u_int32_t last_send = 0;

void setup()
{
	Serial.begin(115200);
	Serial.println();

	// Mux high -> boot select, low -> CAN
	pinMode(CAN_MUX, OUTPUT);
	digitalWrite(CAN_MUX, LOW);

	pinMode(LED_BUILTIN, OUTPUT);
	// attachInterrupt(digitalPinToInterrupt(BUTTON), Button_Down, LOW);

	delay(100);
	init_CAN();
}

void loop()
{
	if (millis() - last_send > 100)
	{
		last_send = millis();
		Button_Down();
	}
}

static void init_CAN()
{
	Serial.println(can1.init(CanSpeed::Mbit1) == HAL_OK
					   ? "CAN: initialized."
					   : "CAN: error when initializing.");

	// FDCAN_FilterTypeDef sFilterConfig;

	// // Configure Rx filter
	// sFilterConfig.IdType = FDCAN_STANDARD_ID;
	// sFilterConfig.FilterIndex = 0;
	// sFilterConfig.FilterType = FDCAN_FILTER_MASK;
	// sFilterConfig.FilterConfig = FDCAN_FILTER_TO_RXFIFO0;
	// sFilterConfig.FilterID1 = 0x321;
	// sFilterConfig.FilterID2 = 0x7FF;

	// can1.configFilter(&sFilterConfig);
	// can1.configGlobalFilter(FDCAN_REJECT, FDCAN_REJECT, FDCAN_FILTER_REMOTE, FDCAN_FILTER_REMOTE);
	can1.activateNotification(&can1RxHandler);

	Serial.println(can1.start() == HAL_OK
					   ? "CAN: started."
					   : "CAN: error when starting.");
}

int dlcToLength(uint32_t dlc)
{
	int length = dlc >> 16;
	if (length >= 13)
	{
		return 32 + (13 - length) * 16;
	}
	else if (length == 12)
	{
		return 24;
	}
	else if (length >= 9)
	{
		return 12 + (9 - length) * 4;
	}
	return length;
}

static void handleCanMessage(FDCAN_RxHeaderTypeDef rxHeader, uint8_t *rxData)
{
	int byte_length = dlcToLength(rxHeader.DataLength);

	Serial.print("Received packet, id=0x");
	Serial.print(rxHeader.Identifier, HEX);
	Serial.print(", length=");
	Serial.print(byte_length);
	for (int byte_index = 0; byte_index < byte_length; byte_index++)
	{
		Serial.print(" byte[");
		Serial.print(byte_index);
		Serial.print("]=");
		Serial.print(rxData[byte_index]);
		Serial.print(" ");
	}
	Serial.println();

	digitalToggle(LED_BUILTIN);
}

static void Button_Down()
{

	static uint8_t press_count = 0;

	press_count++;

	TxHeader.Identifier = 0x321;
	TxHeader.IdType = FDCAN_STANDARD_ID;
	TxHeader.TxFrameType = FDCAN_DATA_FRAME;
	TxHeader.DataLength = FDCAN_DLC_BYTES_2;
	TxHeader.ErrorStateIndicator = FDCAN_ESI_ACTIVE;
	TxHeader.BitRateSwitch = FDCAN_BRS_OFF;
	TxHeader.FDFormat = FDCAN_CLASSIC_CAN;
	TxHeader.TxEventFifoControl = FDCAN_NO_TX_EVENTS;
	TxHeader.MessageMarker = 0;

	TxData[0] = press_count;
	TxData[1] = 0xAD;

	Serial.print("CAN: sending message ");
	Serial.println(can1.addMessageToTxFifoQ(&TxHeader, TxData) == HAL_OK
					   ? "was ok."
					   : "failed.");
}

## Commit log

2023-05-22 lay things out
    [bike_light.kicad_pcb]
2023-05-22 move nmos around
    [bike_light.kicad_pcb]
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2023-05-22 start routing traces
    [bike_light.kicad_pcb]
2023-05-22 add githash label to PCB
    [bike_light.kicad_pcb]
2023-05-22 finish layout
    [bike_light.kicad_pcb]
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2023-06-04 add base layout
    [bike_light.kicad_pcb, servo-drive.kicad_pcb, servo-drive.kicad_sch]
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2023-06-14 layout didn't save without moving the resistors within the vdiv
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2023-06-19 layout checkpoint 1
    [servo-drive.kicad_pcb]
2023-06-21 layout done
    [servo-drive.kicad_pcb]
2023-06-21 add githash to board
    [servo-drive.kicad_pcb]
2023-06-23 add bypass caps to power rail
    [servo-drive.kicad_pcb]
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2023-06-28 Fixed current sensor not connected to ground issue
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2023-07-08 fix switch name
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2023-07-08 add sensor ato file, add v_sens, fix analog sens
2023-07-08 worked out we had the wrong pinout
    [main.cpp]
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2023-07-09 fix duplicate signal/pin names
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2023-07-10 split layouts - take 2
    [servo-drive.kicad_pcb, servo-drive.kicad_sch]
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2023-07-10 import default-build netlist to KiCAD
    [servo-drive.kicad_pcb]
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2023-07-10 power stage component layout complete ish
    [keepout.dxf, nema17_formfactor_outline.dxf, sensor positiion.dxf]
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2023-07-10 Correct Buck-IC Package
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2023-07-10 reverse polarity for XT30 and add LCSC num to BOM
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2023-07-10 layout, more of it
    [servo-drive.kicad_pcb]
2023-07-10 probably sleep deprived drivel
    [servo-drive.kicad_pcb]
2023-07-11 add corner holes
    [servo-drive.kicad_pcb]
2023-07-12 component layout complete, fixed bug with CC2 pin and buck input cap gnd
    [servo-drive.kicad_pcb]
2023-07-12 layout complete
    [servo-drive.kicad_pcb]
2023-07-12 added git hash
    [servo-drive.kicad_pcb]
2023-07-13 more routing progress
    [servo-drive.kicad_pcb]
2023-07-13 Routing almost complete
    [servo-drive.kicad_pcb]
2023-07-13 swap out current sense IC, reduce from 3 to 2, remove split reference opamp
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2023-07-14 add a bunch of visv2 settings
    [servo_drive.vis.yaml]
2023-07-16 Routing complete
    [servo-drive.kicad_pcb]
2023-07-16 Most DRC errors fixed
    [servo-drive.kicad_pcb]
2023-07-17 Upgrade default layout paths
    [servo-drive.kicad_pcb]
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2023-07-23 fix the pin instantiation and signal naming
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2023-07-29 fixed missing 5v conneciton on LED
2023-07-29 fixed LED name for data input pin
2023-07-29 Replace LED with 3x right-angle version
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2023-07-29 Fix LED foorprint
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2023-07-31 lots of dumb little mistaktes
    [servo-drive.kicad_pcb]
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2023-08-02 update positions, apply stubs
    [servo_drive.vis.yaml]
2023-08-06 mechanical outline change
    [board outline.dxf, mechanical keepouts.dxf, servo-drive.kicad_pcb]
2023-08-06 initial component layout
    [board outline.dxf, mechanical keepouts.dxf]
2023-08-07 layout progress, swapped big ol electrolytic for surface mount caps
2023-08-07 library parts
    [Servo v21.step, Servo v22.step]
2023-08-07 layout progress
    [Servo v22.step, servo-drive.kicad_pcb]
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2023-08-08 sync layout with ato src
    [servo-drive.kicad_pcb]
2023-08-08 Placement 90% complete
    [servo-drive.kicad_pcb]
2023-08-08 few bugs, ref shorted to 3v3 in servo drive, current sense not connected
    [servo_drive.vis.yaml]
2023-08-09 swapped out big boi caps for 0805s, finished most of the routing
    [servo-drive.kicad_pcb]
2023-08-09 Fixed footprint for SK6805 LED, was a pain
2023-08-09 added JTAG with Tag connect interface, moved pos sensor to SPI2
    [servo-drive.kicad_pcb]
2023-08-10 playing around with thermal vias
    [servo-drive.kicad_pcb]
2023-08-10 fix SGND on exposed pad, join SGND to GND directly
2023-08-10 Swapped out switch for something smaller
    [servo-drive.kicad_pcb]
2023-08-10 Revert "Merge branch 'jtuma/thermal-vias' into 'wire_up_stm32'"
    This reverts merge request !47
    [servo-drive.kicad_pcb]
2023-08-11 layout improvements, well, getting there
    [servo-drive.kicad_pcb]
2023-08-11 added some more caps, cleaned up layout
    [servo-drive.kicad_pcb]
2023-08-12 swapped to cheaper buck
    [servo-drive.kicad_pcb]
2023-08-12 renamed 10V rail
    [servo-drive.kicad_pcb, servo_drive.vis.yaml]
2023-08-12 Minor cleanup
    [servo-drive.kicad_pcb]
2023-08-12 via gun
    [servo-drive.kicad_pcb]
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2023-09-30 Merge branch 'mawildoer/rejig-inheritance-structure' into 'develop/v1.1.0'
    Refactor existing top-level circuit design
    See merge request atopile/servo-drive!56
    (cherry picked from commit b7e7e3dd762b42cf0fcb014bbbeb24cab568bd95)
    8a86a514 WIP: Refactor existing top-level circuit design
    5f7c1039 Make L6387EDPowerStage compilable and make layout
    41acf5f1 Builds with v0.0.15 compiler
    90a1b85f re-add bleed resistors
    2544efc6 shift default path
    92d2868c re-ref designators - NOTE: some appear to be missing still
    ec3cd0de add halfbridge designators
    4930ca45 remove some crud
    44a4240d Use relative paths in designators
    465bd209 Confirm designator match line-by-line with mainline
    76ad05e6 Match bootst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
    [servo-drive.kicad_pcb, servo-drive.kicad_sch, servo_drive.vis.yaml]
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2023-10-01 Merge branch '25-create-drv8300-powerstage' into 'develop/v1.1.0'
    Create DRV8300 PowerStage and make default for NEMA-17 driver
    See merge request atopile/servo-drive!59
    (cherry picked from commit dc565ce4df3a3593bbe69c314f915e0b8032784e)
    6cb09225 Create DRV8300 Power Stage
    8dac7390 Switch out power stage at the top level
    620f2e74 Add basic rise rate tests
    c3d8bda8 Add p-prefix to all numbered pins
    df571ae1 remove demo test
    231b80dd fix typo on resistor footprint
    7d562036 add pulse power capable resistor
    5382ff5e fix resistor package
    e3ed2e50 clean nettie
    ea5f826b delete redundant file
    4070bca9 typo
    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
2023-10-01 Merge branch '28-switch-to-smaller-button' into 'develop/v1.1.0'
    Resolve "Switch to smaller button"
    See merge request atopile/servo-drive!64
    (cherry picked from commit 53665396a036080a1cd696dffd365e3168a1b14d)
    1fcedaf4 add tiny button in lib
    6b4d9457 totally irelevant but alas
    8169bdac connect things up
    986785b2 nothing to see here
    fc4c25d7 add button to BOM file
    05afc574 clean and consolidate button situation
    6ec522bd Merge branch 'develop/v1.1.0' into 28-switch-to-smaller-button
    4db62663 define No button
    b4c5d13f prototype switch for the micro kit as well
2023-10-01 Merge branch '27-add-jst-gh-2' into 'develop/v1.1.0'
    Add JST-GH
    See merge request atopile/servo-drive!63
    (cherry picked from commit ac3b010103b35113f3282bad606f9eae8ef2ad3c)
    0f95f9b4 add jst GH to lib
    4fed5fae add jst GH files
    afeed0dc fix blank space
    f3c6ba46 connect JST Gh
    87b26352 add JST gh to BOM
    2e1bf572 small cleanups
    4c17baf3 Merge branch 'develop/v1.1.0' of gitlab.atopile.io:atopile/servo-drive into 27-add-jst-gh-2
2023-10-05 progress on layout
    [servo-drive.kicad_pcb]
2023-10-12 Swap uC for STM32G431
2023-10-12 import new stm32 into layout
    [servo-drive.kicad_pcb]
2023-10-14 new board shape and connector positions
    [servo-drive.kicad_pcb]
2023-10-17 Swapped addressable LED pin to SPI MOSI
2023-10-19 routing ~ half way done with DRV8300
    [servo-drive.kicad_pcb]
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2023-11-05 big ol refactor, added lots of interfaces, changed pinout to match moteus controller, layout changed to add more connectors
    [Servo v24.step, servo-drive.kicad_pcb, servo-drive.step]
2023-11-09 Modified micro pinout to match moteus, because they are pretty sick, updated modules to use interfaces where posible, generated netlist and imported to Kicad project
    [servo-drive.kicad_pcb]
2023-11-10 Something fishy is going on with interfaces
    [servo-drive.kicad_pcb]
2023-11-10 fixed githash location, cleaned up silkscreen
    [servo-drive.kicad_pcb]
2023-11-10 Minor silk fixes
    [servo-drive.kicad_pcb]
2023-11-10 renamed step outputs to make Matt happy
    [nema-17-rear-endcap-v1.0.0.step]
2023-11-10 updating board outline
    [board outline.dxf, board_outline.dxf.dxf]
2023-11-10 remove errant numbers excels
    [servo-drive.step]
2023-11-11 fixing reset pin from PB4(TRST) to PG10_NRST
    [servo-drive.kicad_pcb]
2023-11-11 added 100nf caps for current sense opamps
    [servo-drive.kicad_pcb]
2023-11-11 cleaned up silk
    [servo-drive.kicad_pcb]
2023-11-11 cleaned up silk, missed some cheeky designators
    [servo-drive.kicad_pcb]
2023-11-13 updated via sizes to match JLC feedback
    [servo-drive.kicad_pcb]
2023-11-14 fixed via in pad issue + added signal names and test points for debugging
    [servo-drive.kicad_pcb]
2023-11-14 remove old files and add new drawings + cad
    [Servo v21.step, Servo v22.step, atopile_servo_drive.step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]
2023-11-15 silk cleanup and add test points
    [servo-drive.kicad_pcb]
2023-11-17 Update designators and UUIDs in layout
    [servo-drive.kicad_pcb]
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2024-01-24 remove vis files, update ato.yaml, remove ci
    [spin_servo_drive.vis.yaml]
2024-01-24 update the microcontroller
    [servo-drive.kicad_pcb, servo-drive.kicad_sch]
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2024-01-31 relinked designators to layout
    [servo-drive.kicad_pcb]
2024-02-01 fix led name
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2024-03-07 fix typo in filter cutoff
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2024-03-20 adding debug configuration + connecting up current sense
    [atopile_servo_drive.step, servo-drive.kicad_pcb, servo-drive.kicad_sch]
2024-03-22 checkpoint - linking correctly
    [servo-drive.kicad_pcb]
2024-03-22 DRC fixes
    [servo-drive.kicad_pcb]
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2024-03-22 fix duplicate layout in packages
    [programming-headers 2.kicad_pcb]
2024-03-22 removing duplicate layouts for packages
    [ldk220m-r 2.kicad_pcb, ldk220m-r 2.kicad_sch, ma732 2.kicad_pcb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]
2024-03-23 fix designators
    [servo-drive.kicad_pcb]
2024-03-23 moving layout to correct folder
    [servo-drive.kicad_pcb, servo-drive.kicad_sch]
2024-03-23 fix net short issue
    [servo-drive.kicad_pcb]
2024-04-11 added 3D step models
    [servo-drive.kicad_pcb]
2024-04-16 adding step files for components
    [Untitled.kicad_pcb, Untitled.kicad_sch, atopile_servo_drive.step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]
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2024-04-16 removing unused debug config
    [debug.kicad_pcb, debug.kicad_sch]
2024-05-02 swapping MA732 for MT6835 sensor
    [servo-drive.kicad_pcb]
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2024-05-21 flip default select behaviour so button is driving PB8 on boot
2024-05-23 Flip connections around to follow logical flow
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2024-05-23 Flip net-ties to match improved flow
    [servo-drive.kicad_pcb]
2024-05-24 connect missing adc ref to 3v3
2024-05-28 Flip shunts back around to match other layouts
    [servo-drive.kicad_pcb]
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2024-06-22 add clock config with correct wait states and PLL settings. Should work out to 170MHz with 8MHz crystal
    [clock.c]
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2024-07-09 Fix package on buck.input_cap
2024-07-09 Update layout with pullup cap
    [servo-drive.kicad_pcb]
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
